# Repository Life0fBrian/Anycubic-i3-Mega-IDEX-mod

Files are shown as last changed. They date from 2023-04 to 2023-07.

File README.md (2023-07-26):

# Anycubic-i3-Mega-IDEX-mod
This mod converts the Anycubic i3 Mega into an IDEX 3D printer.
all1

The project is currently still in its design phase but already printed to build a first version.
It uses a 1515 aluminum extrusion and MGN12 linear rail for the X gantry.
(The printer itself will get a linear rail mod for the bed as well and upgrades to 24V.)
x_gantry1
x_gantry_rear1

The two independent print heads are driven by 1.8° Nema17 pancake stepper motors to save weight.
It uses E3D compatible V6 hotends with M12 threaded heatsinks and ceramic heating cores to get a small size:
print_heads_close1
The coldend will be cooled by a 30 mm axial fan and the printed model is being cooled by a powerful GDSTIME 4010 radial fan with 12k RPM.

Intention is to print the parts with ASA-CF for more rigidity. But ABS or ASA should be fine as well.

## Features:
- slim print heads
- MGN12 linear rails with MGN12C blocks
- V6 hotends with CHC blocks and threaded heatsinks
- 30 mm coldend fan
- 4010 mm radial fan for part cooling
- endstops on both ends of the X rail and on right print head to have multiple homing options (prefer mechanical micro switches due to better precision)
- bowden setups for light weight print heads

## Electronics:
- You will need a board with at least 7 driver sockets.
- Upgrade to 24 V PSU and board and all fans (mind the heating bed as well!).

## BOM:
- 2 * 30 mm axial fan (5 pack) [GDSTIME](https://aliexpress.com/item/1910412689.html)
- 2 * 4010 radial fan (2 pack) [GDSTIME](https://aliexpress.com/item/1005005094281105.html)
- 2 * threaded heatsink [TriangleLab](https://aliexpress.com/item/32888313090.html)
- 2 * Ceramic Heating Core [TriangleLab](https://aliexpress.com/item/32697889176.html)
- 2 * Nema17 pancake stepper motors [17HE08-1004S](https://www.omc-stepperonline.com/de/e-serie-nema-17-bipolar-1-8deg-17ncm-24-07oz-in-1a-42x42x23mm-4-draehte-17he08-1004s)
- 300 mm MGN12 linear rail with 2 MGN12C blocks
- 300 mm 1515 aluminum extrusion
- M3 heat inserts 
- to be updated...

## Changelog:
- 2023-04-11: Creation of this project
- 2023-04-21: Upload of print heads STLs
- 2023-05-22: Upload of left and right X axis mounts and respective motor mounts
- 2023-05-28: Replaced X axis mounts with v2 versions and corrected linear bearing diameter (reference Anycubic i3 Mega model was wrong here)
- 2023-06-16: Updated right motor mount (more rigid pulley stand off) and added mod for Y axis tensioner for use of original bed/linear rails.
- 2023-07-25: Upload of left and right waste bucket and mould for the nozzle lips.
- 2023-07-26: Updated README.md with latest pictures.

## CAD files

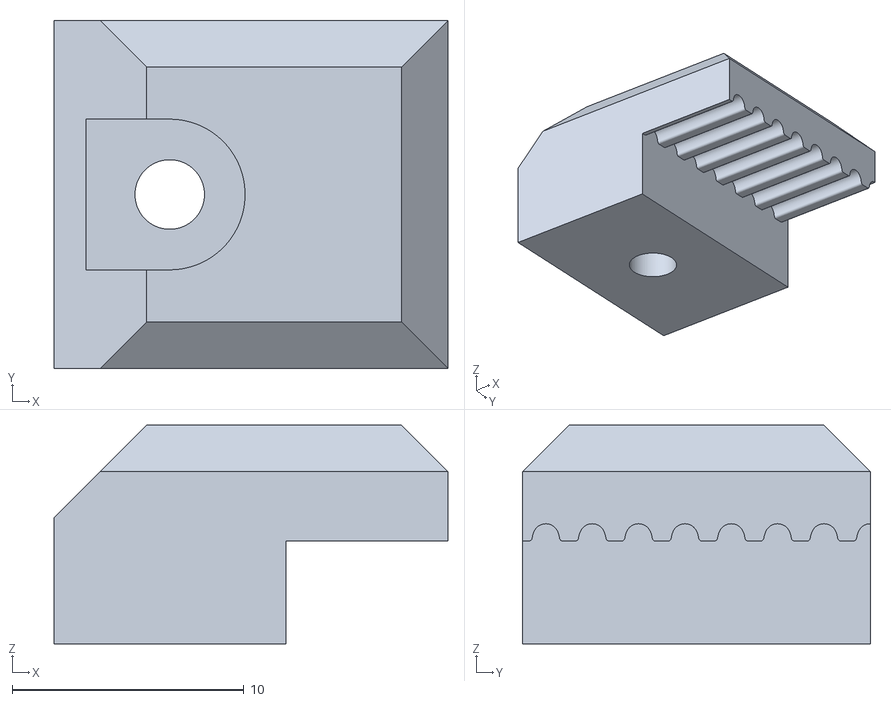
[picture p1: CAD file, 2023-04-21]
STL/PRINT_HEAD/belt_clamp_left_v1.stl
17.0 x 15.0 x 9.43

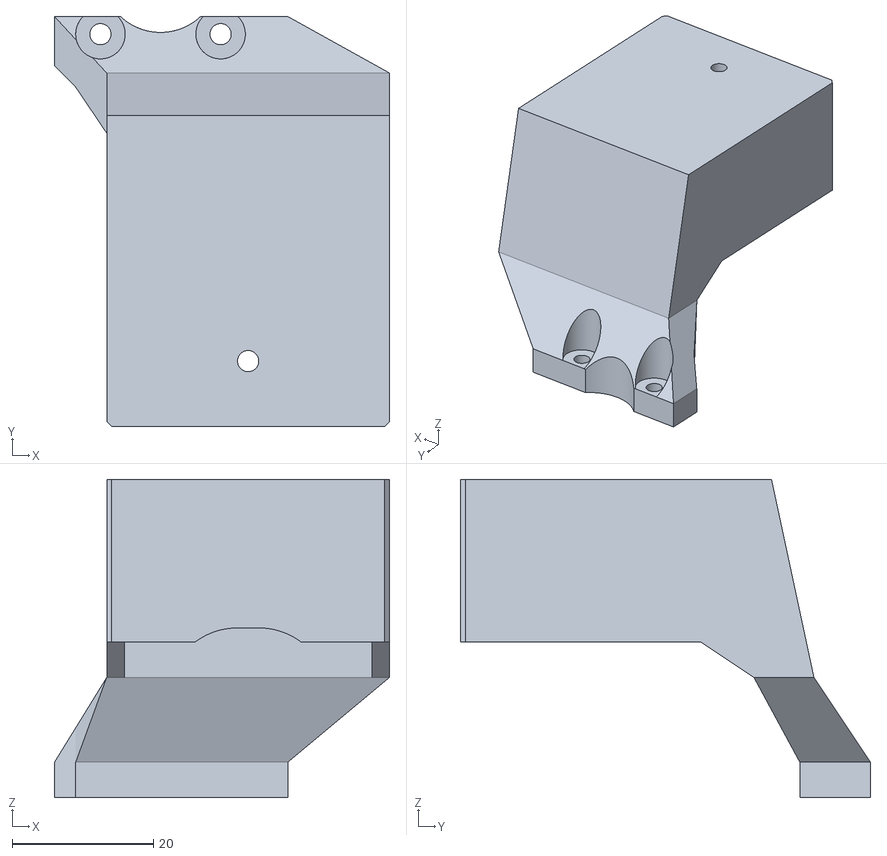
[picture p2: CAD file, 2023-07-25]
STL/WASTE_BUCKETS/right_waste_bucket.stl
47.4 x 58.0 x 45.0

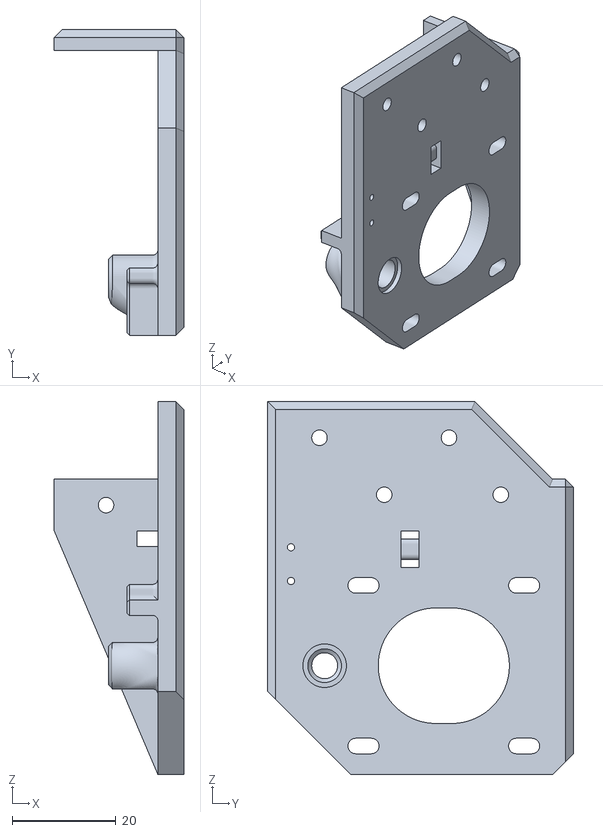
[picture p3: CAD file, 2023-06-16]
STL/X_AXIS/x_motor_mount_right_v2.stl
25.0 x 59.0 x 72.0

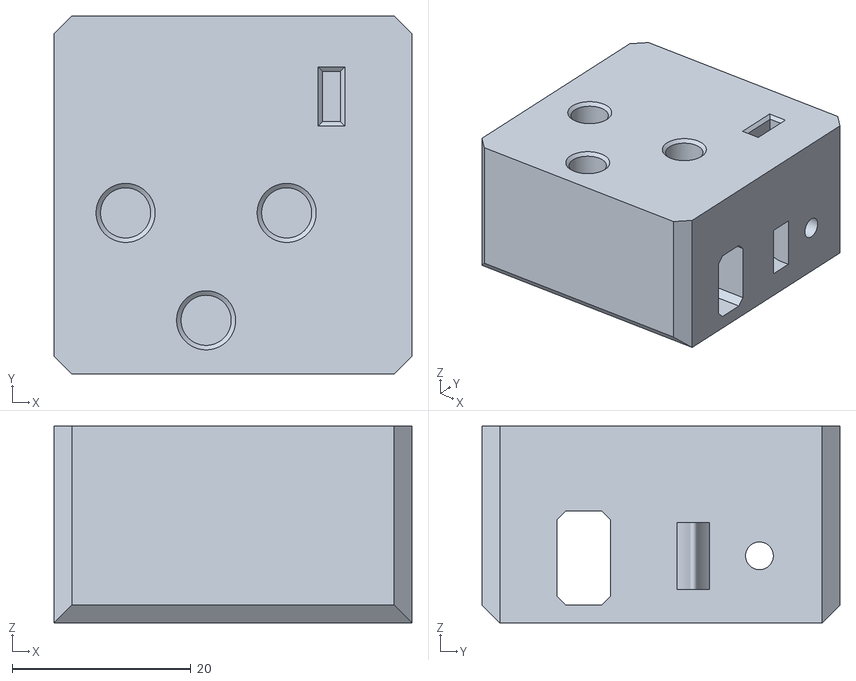
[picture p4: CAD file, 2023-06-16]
STL/Y_AXIS_TENSIONER/y_tensioner_housing_short.stl
40.0 x 40.0 x 22.0

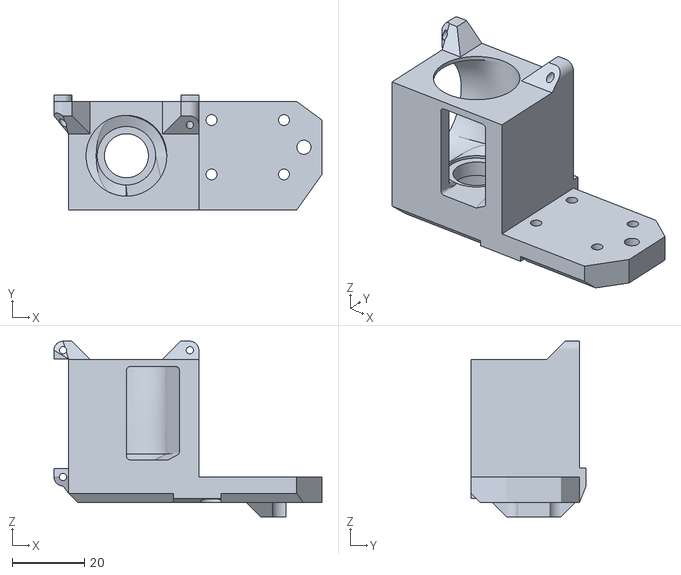
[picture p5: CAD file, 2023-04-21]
STL/PRINT_HEAD/print_head_right_v1.stl
74.0 x 31.8 x 48.5

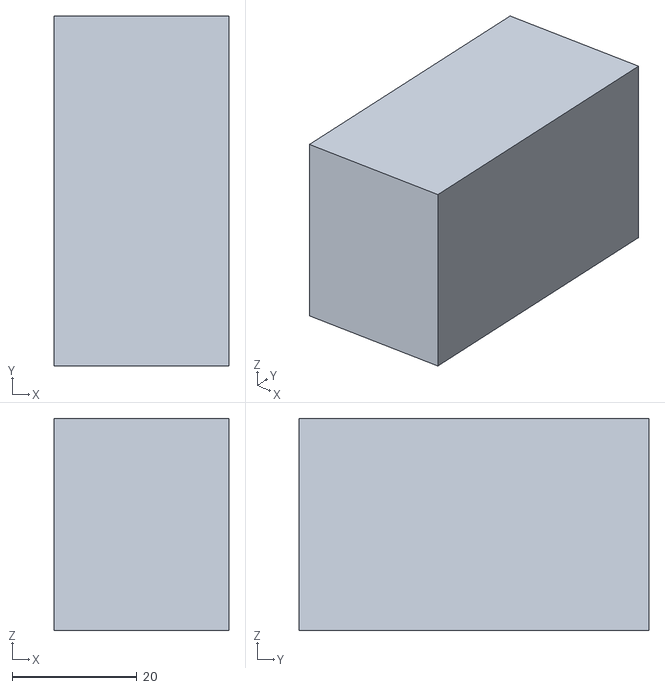
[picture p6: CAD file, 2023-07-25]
STL/WASTE_BUCKETS/lip_mould.stl
28.0 x 56.0 x 34.0

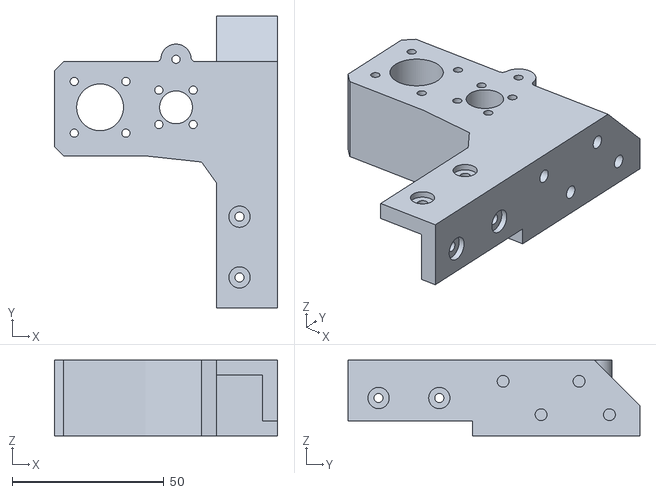
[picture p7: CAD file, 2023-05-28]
STL/X_AXIS/x_mount_right_v2.stl
73.4 x 96.0 x 25.0

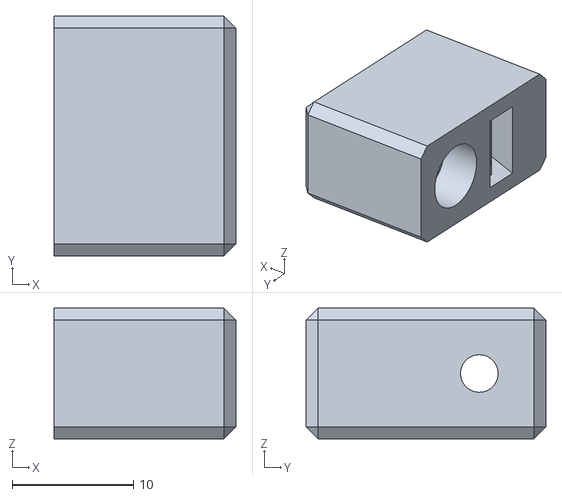
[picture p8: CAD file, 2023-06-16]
STL/Y_AXIS_TENSIONER/y_tensioner_spanner_short.stl
15.0 x 19.8 x 10.8

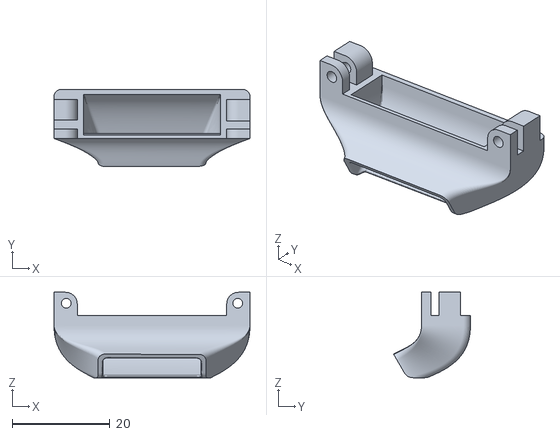
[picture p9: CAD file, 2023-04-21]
STL/PRINT_HEAD/fan_duct_left_v1.stl
40.0 x 15.7 x 17.5

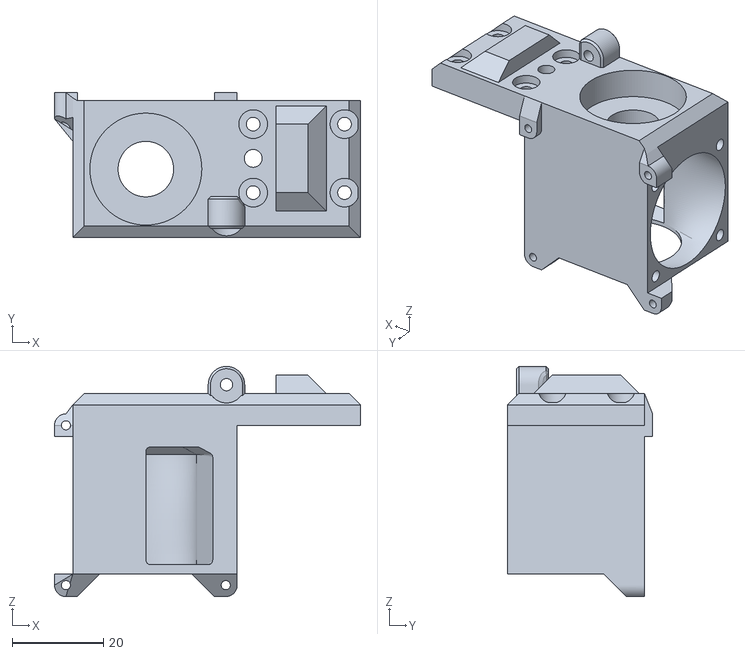
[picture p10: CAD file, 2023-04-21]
STL/PRINT_HEAD/print_head_left_v1.stl
67.0 x 31.8 x 50.4

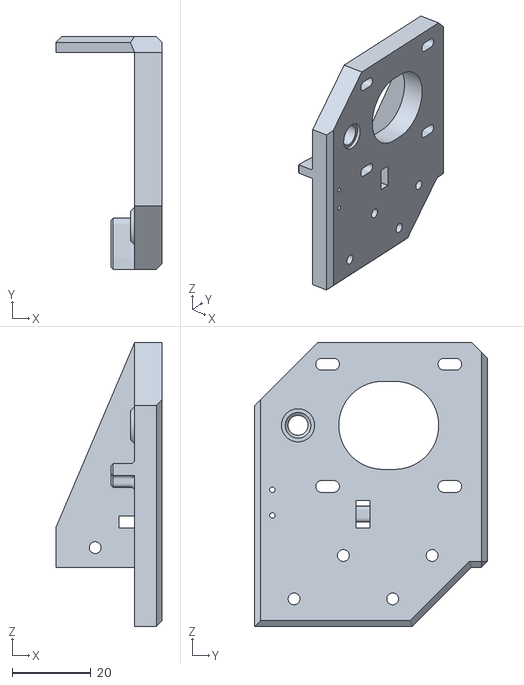
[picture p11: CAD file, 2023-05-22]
STL/X_AXIS/x_motor_mount_left.stl
27.0 x 59.0 x 72.0

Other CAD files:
STL/WASTE_BUCKETS/left_waste_bucket.stl
STL/X_AXIS/x_mount_left_v2.stl
STL/PRINT_HEAD/fan_duct_right_v1.stl
STL/PRINT_HEAD/belt_clamp_right_v1.stl

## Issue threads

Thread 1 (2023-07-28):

z regulation of second extruder

ccomincini, 2023-07-28:
Hi how do you trim the z height dfference between first and second rinthead for fine calibration?

Life0fBrian, 2023-07-29:
Hi,

I've done this using aluminum foil or feeler gauge tape with different thicknesses.
Before the trimming process you home z and level your bed and then you can use a feeler gauge to determine the difference between the nozzles.

Closed 2023-10-09.

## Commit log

2023-04-11 Create STL
2023-05-28 Delete x_mount_left.stl
    wrong diameter for linear bearing
    [x_mount_left.stl]
2023-05-28 Delete x_mount_right.stl
    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
    [x_mount_right.stl]
2023-05-28 Add files via upload
    fixed diameter for linear bearing
    [x_mount_left_v2.stl, x_mount_right_v2.stl]
2023-06-16 Add files via upload
    Added support for pulley stand off.
    [x_motor_mount_right_v2.stl]
